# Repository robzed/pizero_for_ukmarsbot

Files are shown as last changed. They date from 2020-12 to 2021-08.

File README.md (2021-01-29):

# Pizero for ukmarsbot
Adding a Rapberry Pi Zero onto the UK Mars Bot

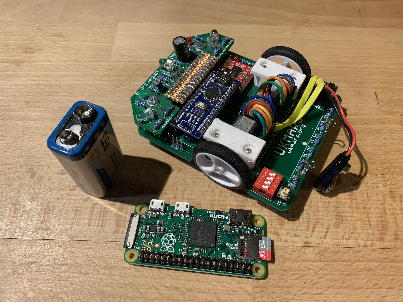
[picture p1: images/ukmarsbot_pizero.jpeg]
UKMarsBot and Pi Zero

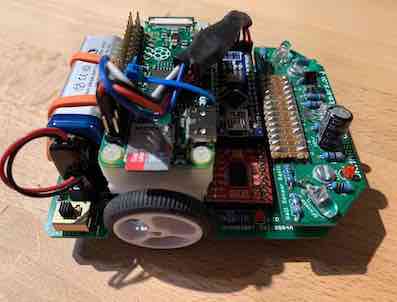
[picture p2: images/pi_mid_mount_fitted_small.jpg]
UKMarsBot_and_Pi
]

NOTE: 

# Background
The UKMarsBot is a maze solver and line follower, designed by the UK Mars and Robotics Society (UKMars). It has a Arduino Nano attached as the standard microcontroller. 

 - GitHub Project page: https://github.com/ukmars/ukmarsbot
 - UKMars Project page: https://ukmars.org/projects/ukmarsbot/
 - Building instructions for the UKMarsBot https://github.com/ukmars/ukmarsbot/wiki

This project aims to add a Raspberry Pi Zero to that basic design.

There is a provisional scope document here UKMARSPIBOT_enhancement_scope.pdf

There is a related seperate GitHub project for the Arduino Nano I/O coprocessor software: https://github.com/robzed/ukmarsey 

# Methods

There are two potential methods of connecting a Raspberry Pi Zero to the UKMARSbot:

1. Produce an adapter board that converts the Pi Zero header to the Arduino Nano footprint, completely replacing the Ardunio Nano. 
2. Connect the Raspberry Pi to the Arduino over a serial interface to the existing Arduino Nano and use the Nano as an I/O processor.

This article will examine the **second** option since this is the simpler option to construct, without a custom PCB. (There are, however, some notes on method 1 provided in '[Replacing the Arduino Nano Entirely](Documentation/Nano_Replacement.md)'.)

# Parts required 
  - UKMarsBot - tested working with Arduino Nano
  - Arduino Nano v3 (or equivalent third-party Nano)
  - Pi Zero v1.3

We will be using a Pi Zero (not a Pi Zero W which uses more power).

# Table of Contents
 - [Powering the Pi Zero … 5v Power … consideration on power](Documentation/Power_Requirements_Detail.md)
 - [What are the options for communicating between Pi Zero and Arduino Nano?](Documentation/Connections_Options.md)
 - [Summary of Electrical Connections between Pi Zero and Arduino Nano](Documentation/Connections_UART_Detail.md)
 - [Installing the Pi Zero Operating System](Documentation/Install_PiZero_OS.md)
 - [Logging into the PI](Documentation/Logging_into_Pi.md)
 - [Disable Linux Console on UART](Documentation/Disable_Linux_Console_on_UART.md)
 - [Scripting language for the I/O processor](Documentation/Pi_and_Nano_Software.md)
 - [Mechanical Mounting - Mounting the Pi Zero onto UKMarsBot](Documentation/Mechanical.md)
 - [Software for the Pi Zero](Documentation/Pi_Zero_Software.md)
 - [Shutdown down the Pi Zero](Documentation/Shutdown_Pi_Automatically.md)
 - [Upgrading the Pi Zero Operating System](Documentation/Upgrading_the_operating_system.md)

# Advanced Topics (Not finished)
 - [Using a Pi Zero W instead of a Pi Zero](Documentation/Pi_Zero_W.md)
 - [Programming the Nano from the Pi Zero](Documentation/Programming_the_Nano.md)
 - [Speed up the Raspberry Pi Boot](Documentation/Speed_up_Pi_Boot.md)
 - [Real time processing on the Raspberry Pi](Documentation/Pi_Real-Time.md)
 - [Reducing Pi Zero Power consumption](Documentation/Reducing_Power_Consumption.md)
 - [Replacing the Arduino Nano Entirely](Documentation/Nano_Replacement.md)
 - [Crazy and Wierd ideas](Documentation/Other_Crazy_Ideas.md)
 - [Remote Debugging Python on a Robot](Documentation/RemoteDebuggingPython.md)

# Other Topcs
 - [Sharing the Internet via OTG](Documentation/Sharing_your_internet_OTG.md)

# Future
 - Increasing the 5v power available to the Pi
 - Fitting a camera

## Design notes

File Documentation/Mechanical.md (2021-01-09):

# Mechanical Mounting - Mounting the Raspberry Pi Zero onto UKMarsBot

To mount the Raspberry Pi securely requires some 3d Printing work.

The design here uses two parts - new motor mounts and the Pi Zero holder which is attached to the motor mounts. These are generated by OpenSCAD using the file ***'rpi_ukmarsbot_mount.scad'***

There are two options provided here (see photos below):
 - A front mount - over the Arduino. This keeps the motors clear, but increases the weight at the front of the Robot - which often is heavy already with sensors. The mini USB connector of the Arduino is still accessible, but the Arduino reset is covered.
 - A mid mount - over the Motors. This means that the weight is more equally distributed over the wheels and this doesn't increase the front weight as much. Any access to the motors or encoders involves removing the Pi Zero.

It might be possible to do a rear mounted, over the battery - but that isn't provided here. 

If you are re-generating the STL files from the OpenSCAD file (say after making a change), the control is generated by the following three settings towards the bottom of the file:
```
SELECT_PI_PLATE_FRONT = false;
MOTOR_MOUNTS = false;
SELECT_PI_PLATE_MID = true;
```
You can also see the whole assembly by selecting the motor mount and one of the two plates.

These are pre-generated STL files:
 * pi_plate.stl (front mount)
 * motor_mounts_only.stl (motor mounts with extra height and holes to fix plates)
 * pi_plate_mid_placement.stl (mid mount)

For fixings, I used M2.5 nylon screws to fix the Pi Zero to 'Pi Plate', and M2 9mm metal screws to fix the Pi plate to the motor mounts. These were fitted screwing into the 3D printed PLA - basically holding by friction fit - it might require some tuning for your specific application. For instance you might need to reduce the holes slightly, or use self-tapping screws.

# Pictures for the Mid Raspberry Pi Mount

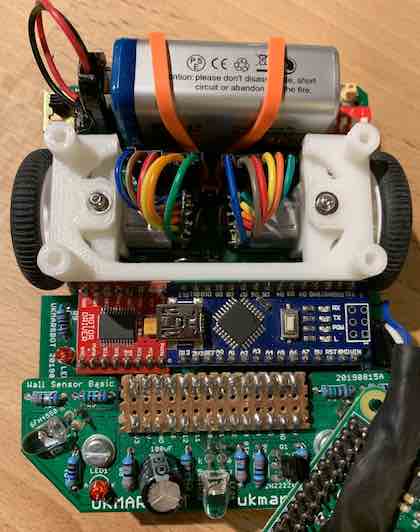
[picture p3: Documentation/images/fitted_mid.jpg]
Fitted Mid

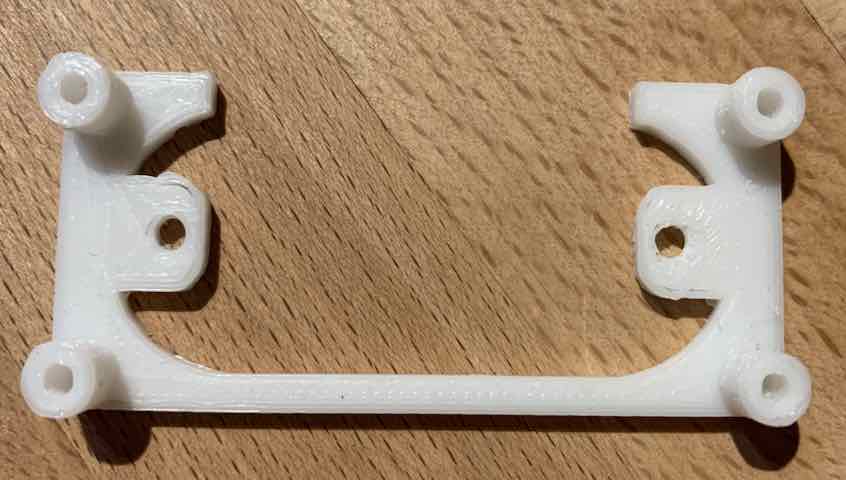
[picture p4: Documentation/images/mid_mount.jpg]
Mid Mount

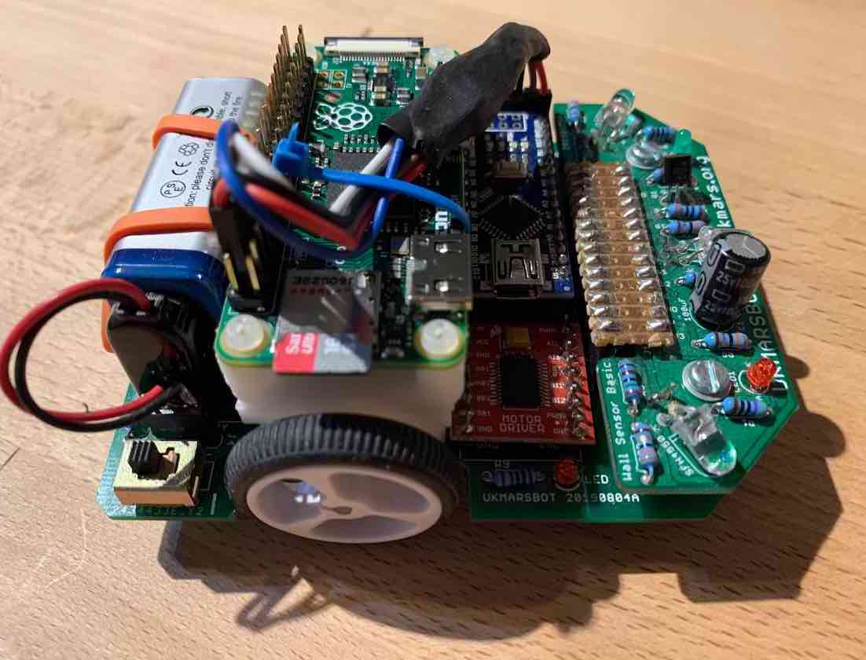
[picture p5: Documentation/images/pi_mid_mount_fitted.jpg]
Mid Fitted 1

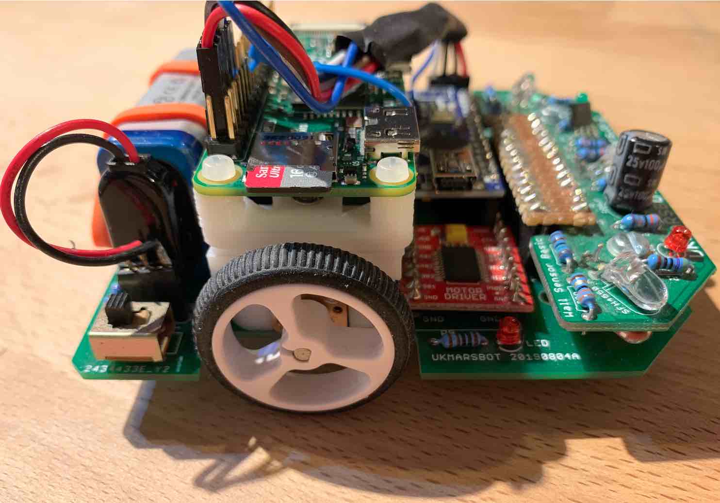
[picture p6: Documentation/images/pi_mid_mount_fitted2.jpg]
Mid Fitted 2

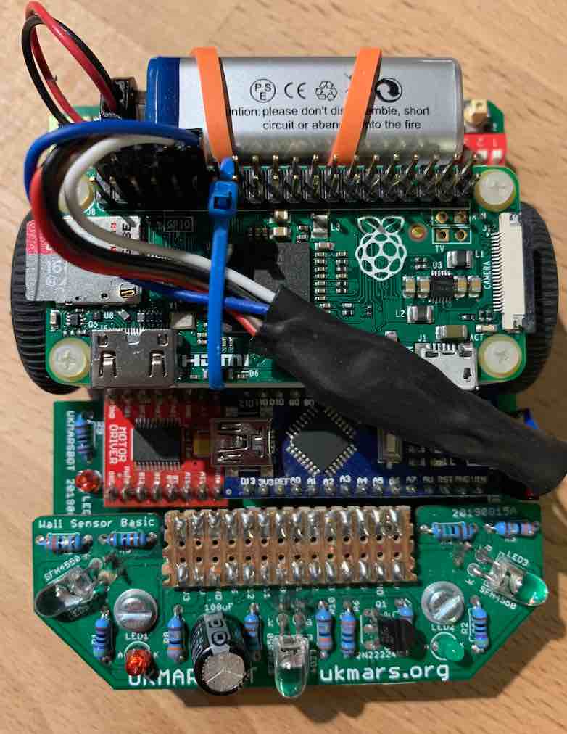
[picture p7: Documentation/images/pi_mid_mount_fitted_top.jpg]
Mid Fitted Top

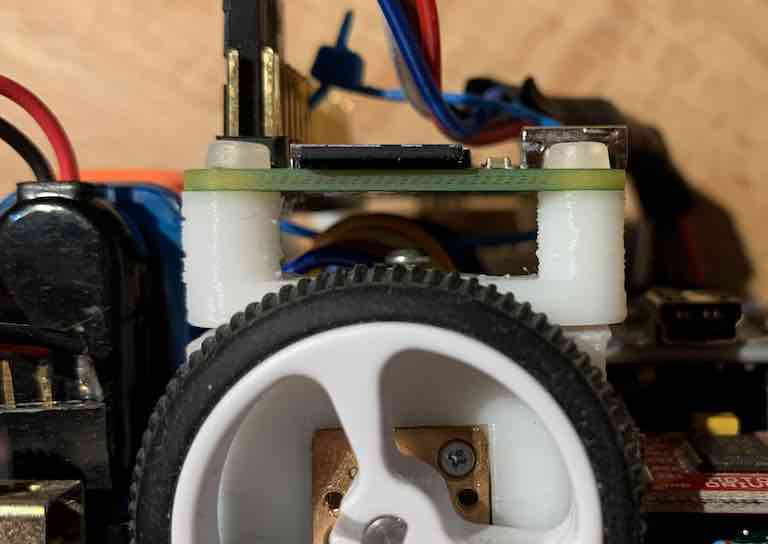
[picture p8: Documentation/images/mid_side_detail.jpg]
Mid Side Detail

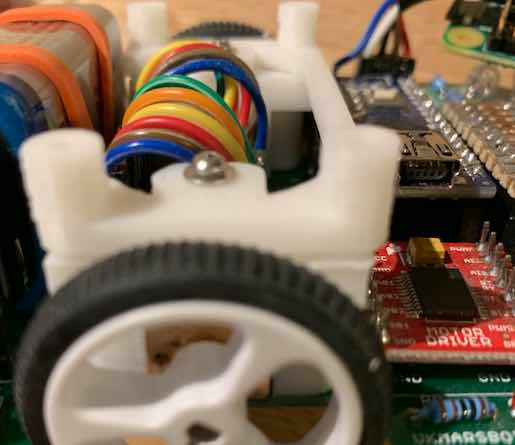
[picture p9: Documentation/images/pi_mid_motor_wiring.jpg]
Motor Wiring


# Pictures for the Front Raspberry Pi Mount

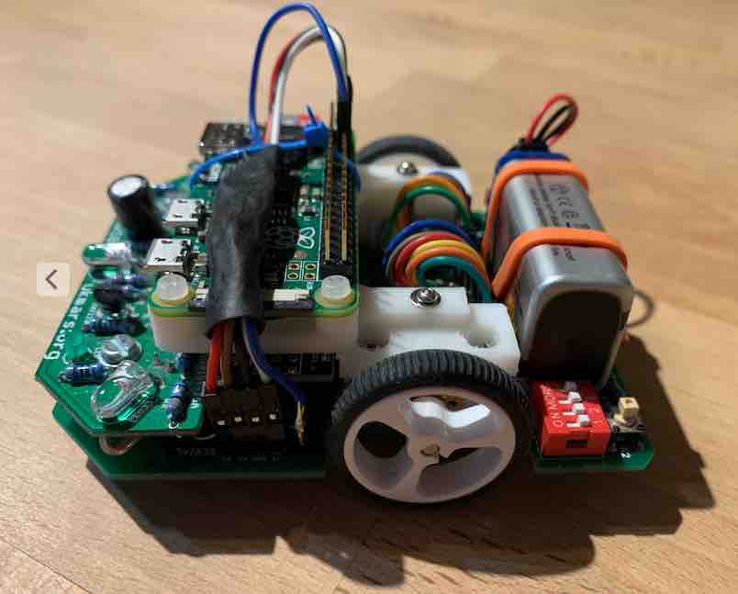
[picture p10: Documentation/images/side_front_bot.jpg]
Side Front Robot

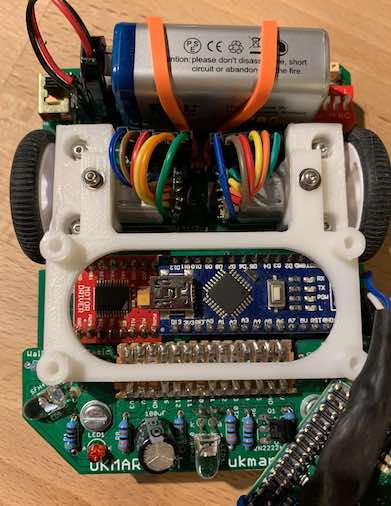
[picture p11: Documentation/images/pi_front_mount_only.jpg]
Front Mount Only

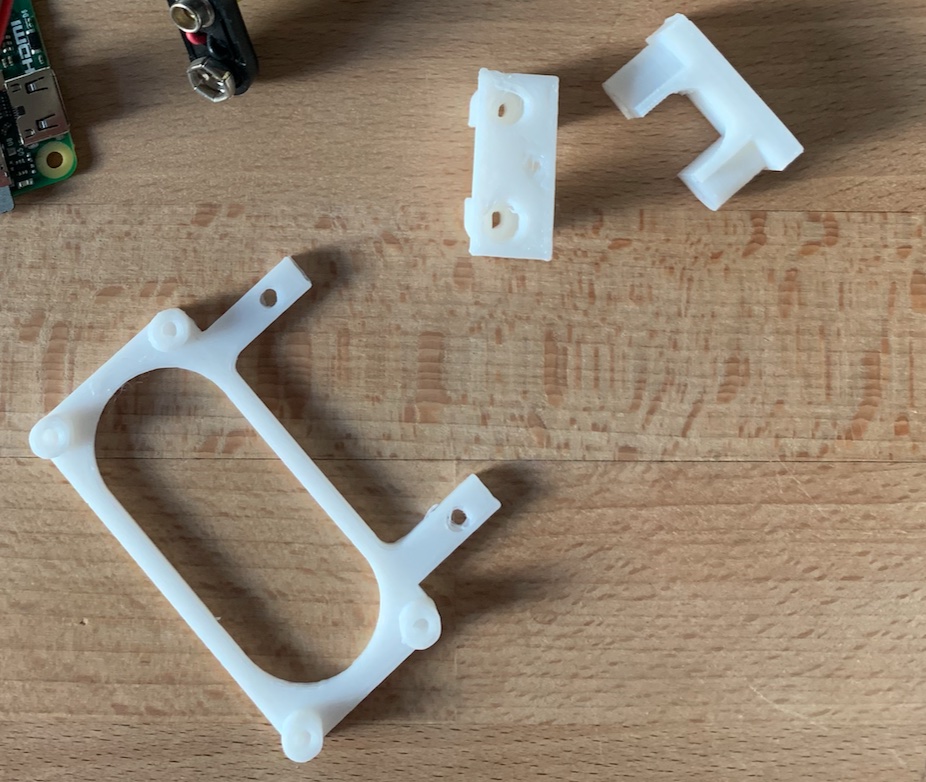
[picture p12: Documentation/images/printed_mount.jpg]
Printed Mount

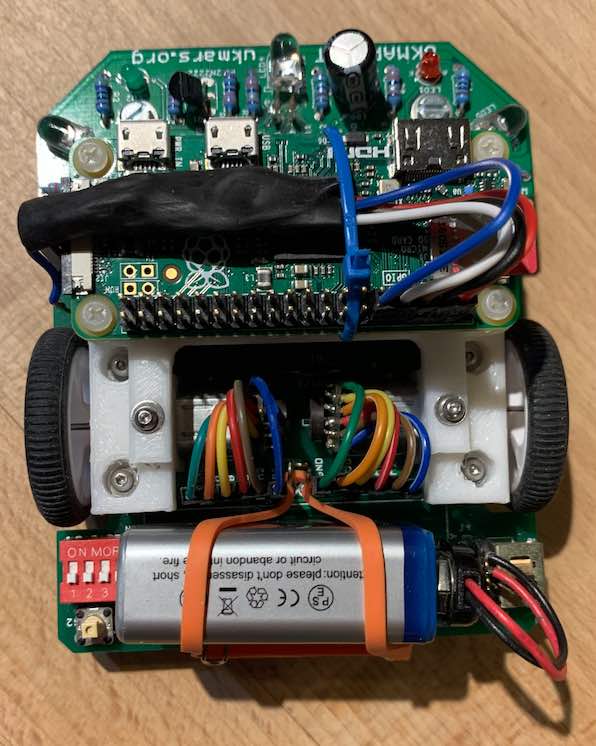
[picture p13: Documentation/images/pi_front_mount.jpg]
Front Mount

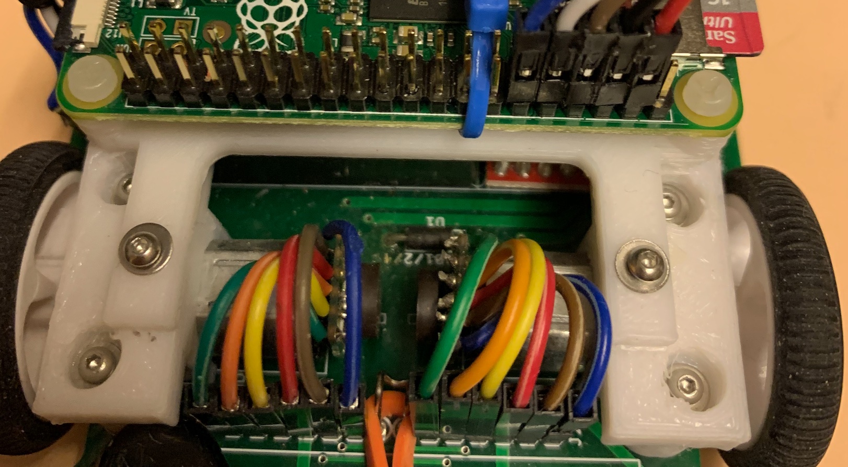
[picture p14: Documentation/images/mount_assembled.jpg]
Mount Assembled

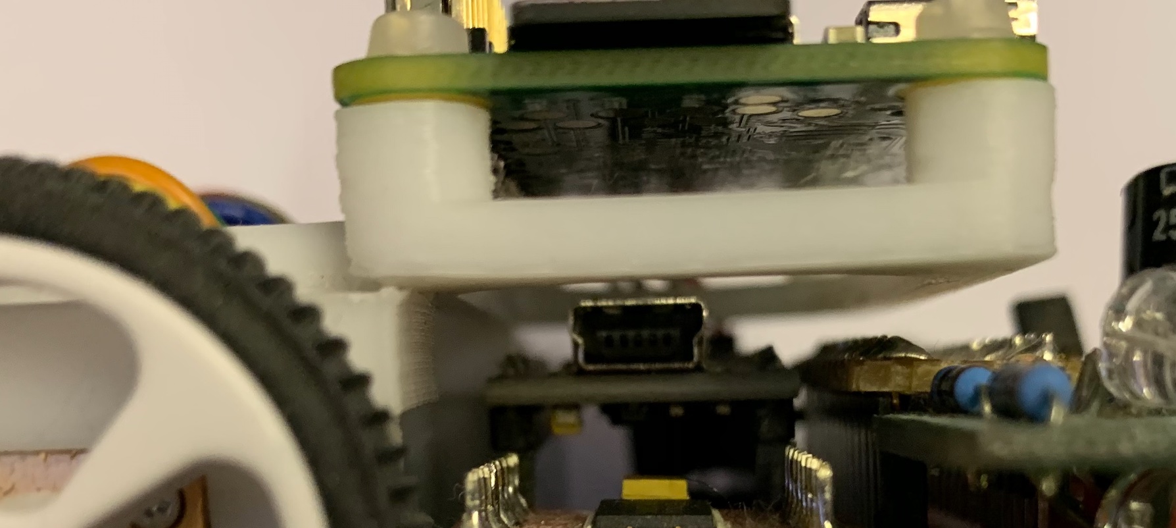
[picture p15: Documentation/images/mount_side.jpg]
Mount Side


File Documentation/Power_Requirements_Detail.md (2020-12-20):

# Powering the Pi Zero

We will power the Pi Zero with 5 volts. The Arduino Nano itself has 5v regulator part number LM1117IMPX-5.0 for the new ones (v3), **Does this have enough additional current to power the Pi?**  Notice some third-party Nano’s use the AM1117-5.0, so we will consider that as well (this is a similar part). 

This is a _linear_ regulator - so the power dissipation is higher when the input voltage is bigger, and it needs to be at least 6.3v for higher currents, otherwise the regulator will start dropping out.

Older Arduino Nano’s used a different regulator - part number UA78M05 - this required 7v input minimum before it stopped regulating properly, and additionally might have different power dissipation. No calculation has been done here.

## Current into the Pi Zero at 5v

The average current of the Pi Zero v1.3 running command line with no GUI, with nothing connected and the HDMI disabled is about 100mA @ 5v, although it might higher on boot - we should assume at least twice that to be safe. It’s possible to reduce that to 80mA by for instance, disabling HDMI.

Please see '[Reducing Power Consumption](Reducing_Power_Consumption.md)' for other details.

Powering the Raspberry Pi Zero doesn’t need to be via the PWR IN Micro-USB power-  we can do this via the 40 way header - pins 2 and 4 are connected to the 5v rail. (Obviously we need to connect the ground / 0v pins as well).

## Calculating the power available for the Raspberry Pi from the Ardunio regulator:

Total current **theoretically** available using LM1117IMPX-5.0 = 800mA

Total power **theoretically** available using AM1117-5.0 = 1A

However, the limiting factor is the power dissipation of the package. Since they are linear regulators they get rid of the ‘extra voltage’ (actually extra power) by dissipating it as heat. If you run your UKMARSbot with a Nickel Metal Hydride 9v battery, then it might (when fully charged) sit at 9v (on load, offload it can be higher) - although normally it's about 8.5v. To get down to 5v involves getting rid of all 4v times the current in heat. This is because P = IV (Power equals current times voltage).

The current of the Arduino is probably something like 33mA@5v (or 167mW), but we also need to take account of all 5v and 3v3 usage of the UKMARSBot. This adds up to about 49 mA to 66mA depending upon LEDs @ 5v. (The Arduino can theoretically use I/O to up 233.4mA as well, and we have to assume you don’t leave the IR LEDs on all the time…)

https://arduino.stackexchange.com/questions/926/what-is-the-maximum-power-consumption-of-the-arduino-nano-3-0

The currents looks well within the limits of the 5v regulator - even during boot up, but we also need to consider power dissipation. 

The LM1117 data sheet has a graph  “Figure26. Maximum Allowable Power Dissipation vs Ambient Temperature for SOT-223”. If the ambient temperature is 25 degrees C, then we can get between 800mW and 1.4W depending upon how good the heat sink created by ground plane  - and usually it’s not as good!

At 800mW, dissipating 4v (worst case) at 100mA for the  Pi Zero (Let’s ignore the initial boot up current - and assume the regulator will take a while to get up to 125 degrees C), and then 66mA for the Ardunio and I/O, sensors, etc. 

So 166mA * 4v = 664mW. This gives us some margin (20%) assuming that the power dissipation of the package on this PCB is 800mW. 

NOTICE: The regulator part (which is located on the underside of the Arduino Nano) might get hot at this current - and care should be taken to avoid getting burnt - but usually it’s out of reach when plugged into the UKMarsBOT.

## Other Power notes

The Pi Zero v1.3 has a PAM2306AYPKE, which is a buck regulator for 1.8V/3.3V. Buck regulators are quite efficient (to up 96%) and this means lower currents. NOTE: Earlier Raspberry Pi’s had linear regulators - and these will lead to higher currents. 

Other peripherals (cameras, keyboards, mice, etc.) will greatly increase power usage and current drawn. Do not connect cameras and record video! https://raspi.tv/2017/how-much-power-does-pi-zero-w-use

## IMPORTANT NOTE

If you want to use more features on the Pi Zero, or a Pi Zero W (and Bluetooth from computer and mobile phone is cool, as is a network) - then you will need to calculate whether there is enough current avaialble at 5v, or add a second regulator.

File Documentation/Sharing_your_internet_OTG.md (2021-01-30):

# Sharing your Internet with the Pi Zero via OTG

## Mac

System Preferences > Internet Sharing

First you have to select RNDIS/Ethernet Gadget then Internet Sharing

Make sure you have selected where you have sleected where to share your internet connection from!

https://raspberrypi.stackexchange.com/questions/47678/rndis-ethernet-gadget-share-internet

NOTE: Internet sharing can stop sleep while enabled, especially if connected to AC Power.

## Windows

**todo**

## Linux Dekstop

**todo**

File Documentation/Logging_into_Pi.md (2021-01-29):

# Logging into the PI

Obviously you could connect to the Raspberry Pi with a monitor, keyboard and mouse - but this is a bit pain.

Since we’ve used the UART for communication to the Ardunio Nano, we can’t log in via serial either.

However, the Pi Zero (only) supports OTG mode, where you can connect it directly to the USB of your computer and access via SSH or VNC. To do this you need to prepare the SD card before you boot it:

For this method, alongside your Pi Zero you will require:
 - MicroUSB cable (USB-A one end to insert into your computer, micro-USB another - to insert into the Pi Zero),
 - MicroSD card (that you programmed with Raspberry Pi OS),
 - a computer which can be running Windows (with Bonjour, iTunes or Quicktime installed), Mac OS or Linux (with Avahi Daemon installed, for example Ubuntu has it built in).

Then do the following:

1. Once Raspbian is flashed, open up the boot partition (in Windows Explorer, Finder etc) and add to the bottom of the 'config.txt' file dtoverlay=dwc2 on a new line, then save the file.
2. If using a recent release of Jessie (Dec 2016 onwards), then create a new file simply called ssh in the SD card as well. By default SSH is now disabled so this is required to enable it. Remember - Make sure your file doesn't have an extension (like .txt etc)!
3. Finally, open up the cmdline.txt. Be careful with this file, it is very picky with its formatting! Each parameter is seperated by a single space (it does not use newlines). Insert modules-load=dwc2,g_ether after rootwait. To compare, an edited version of the cmdline.txt file at the time of writing, can be found in the references below.
4. That's it, eject the SD card from your computer, put it in your Raspberry Pi Zero and connect it via USB to your computer. It will take up to 90s to boot up (shorter on subsequent boots). It should then appear as a USB Ethernet device. You can SSH into it using raspberrypi.local as the address.

## Some references:
- https://gist.github.com/gbaman/975e2db164b3ca2b51ae11e45e8fd40a
- https://blog.gbaman.info/?p=791
- https://raspberrypi.stackexchange.com/questions/38827/how-to-connect-raspberry-pi-zero-to-pc#38828
- https://www.novaspirit.com/2016/10/18/raspberry-pi-zero-usb-dongle/

If you are using *Windows*, you’ll need to install Bonjour.

You can connect to the Rasberrry with a USB cable with a microUSB end plugged into the USB Pi Zero connection (NOT PWR IN). NOTE: Make sure it’s a data cable, not just a charge cable. (One way to test this is to use a Android phone with the cable …)

Because of Bonjour, you can probably directly SSH into the Pi Zero.

More information here especially about Windows: https://learn.adafruit.com/turning-your-raspberry-pi-zero-into-a-usb-gadget/ethernet-gadget

To SSH into your Raspberry Pi you can do this on Linux and Mac

    ssh pi@raspberrypi.local

On Windows, you can use any program that supports SSH, for example Putty, WinSCP, or Teraterm. The address should be raspberrypi.local and the user is 'pi'. 

Password will be default **raspberry**

NOTE: It will give you a warning, since we are using the default password.

The time and date will not be set. If this bugs you, type:

    sudo date -s "6 Dec 2020 22:36"

If the board gets network access, then NTP will synchronise the time.

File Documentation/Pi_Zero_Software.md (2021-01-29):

# Pi Zero Software

# Summary

Jobs need to be split between the Arduino Nano and the Raspberry Pi Zero.

We want to use the Raspberry Pi processing power and large RAM to do as much as possible, but there are some constraints we need to be aware of as we design the software:
 - We don't have instance access to the sensors and motors from the Pi Zero, and this means we need to do fast operations with low latency on the Arduino Nano.
 - We need to make sure that the Raspberry Pi isn't busy which holds up commands to the Arduino Nano.
        - The SD Card especially is slow to read and write and can delay the program.
 - The serial link between the Pi Zero and Nano is slow - and therefore:
    - Introduces latency between sensor data and actions
    - We need to make sure sensor data and commands are as small as possible. (It will be nice to make them human readible, however, for ease of debugging).
 - The basic Nano only has 2 KByte of RAM and 32 KByte of Flash. 
   - (Although the Arduino Nano has 1KByte of EEPROM, it seems useless when we have an SD Card on the Raspberry Pi - as long as we defer writes till after runs.?)
 - The Pi Zero only has a single processor.
 - The UART is full-duplex (can send and receive simulataneously) - and we should leverage this to minimise latency.

# Overview
The Pi Zero needs software to:

 * Talk to the Ardunino and tell it what to do
 * Process information from the Arduino (e.g. batteries, sensors, switches, etc.)
 * Decide when to stop (e.g. when batteries are too low, or we have complete the mission).
 * Decide when to shutdown the Pi Zero.

# Setup Python serial library

We will use Python 3 here. If you try to import serial you will probably get an error:

    python3
    pi@raspberrypi:~ $ python3
    Python 3.7.3 (default, Jul 25 2020, 13:03:44) 
    [GCC 8.3.0] on linux
    Type "help", "copyright", "credits" or "license" for more information.
    >>> import serial
    Traceback (most recent call last):
      File "<stdin>", line 1, in <module>
    ModuleNotFoundError: No module named 'serial'
    >>> quit()

So you'll need to install it for Python 3. Let's do it via pip3. You need network access - so if you are just using on the OTG you need to make sure you have network access. There is information here [Sharing the Internet via OTG](Documentation/Sharing_your_internet_OTG.md)

    sudo apt-get install python3-pip

Then install pyserial

    sudo pip3 install pyserial

Then:

    pi@raspberrypi:~ $ python3
    Python 3.7.3 (default, Jul 25 2020, 13:03:44) 
    [GCC 8.3.0] on linux
    Type "help", "copyright", "credits" or "license" for more information.
    >>> import serial
    >>> port = serial.Serial("/dev/serial0", baudrate = 115200, timeout = 0.1)
    >>> print(port)
    Serial<id=0xb6687d10, open=True>(port='/dev/serial0', baudrate=115200, bytesize=8, parity='N', stopbits=1, timeout=0.1, xonxoff=False, rtscts=False, dsrdtr=False)
    >>> port.inWaiting()
    0

If you have a problem accessing the serial, you might need to give the 'pi' user access - the group is 'dialout'. You can check with the groups command. 

    pi@raspberrypi:~ $ groups
    pi adm dialout cdrom sudo audio video plugdev games users input netdev gpio i2c spi

You can add the 'pi' to the group with:

    sudo adduser pi dialout

For other users replace pi with the user name. 

**(This is not finished yet)**

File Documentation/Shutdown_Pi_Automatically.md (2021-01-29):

# Shutting Down the Raspberry Pi Automatically

If you just turn the switch off the UK Mars Bot, then there is some chance - if it’s written to the SD card (always possible) that you will corrupt the SD card and will need to refresh it. 

Obviously you could plug in a USB cable and issue “sudo shutdown -h now” or “sudo poweroff”, but it’s not very convenient. (Wait for the LED to stop flashing and go out).

It’s much better to read the switches on the UKMARSBot and shutdown the Pi Zero that way - based on the program in the Raspberry Pi. This can either be by the press-button or switches, but also probably needs to be when the battery is low.

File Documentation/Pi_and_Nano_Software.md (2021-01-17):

# Getting the New Nano+Pi Zero to do some stuff

We will use a low overhead serial protocol based on the command line here https://github.com/robzed/ukmarsey

Please visit that project for details - this what needs to be programmed into the Arduino Nano for the robot to function.

The Python program in this project will talk to that software.

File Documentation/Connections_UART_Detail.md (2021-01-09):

# Summary of Electrical Connections between Pi Zero and Arduino Nano

The basic connections are: 

 1. Ground - ideally several ground points will prevent problems with power and data
 2. 5v
 3. TX - data transmit
 4. RX - data receive

NOTE: This leaves many pins free for other uses on the Raspberry Pi Zero!

Connection header - The UK MARS Bot provides a 4 pin header with the above connections. Although it only contains a single ground, it’s probably good enough to experiment with as long as the header is tight.

Nano TX / Pi Zero - voltage conversion to protect the Pi Zero receive - two resistors will change the voltage level from 5v on the Nano to 3v on the Raspberry Pi. 3k3 ohm connected to ground, 2k2 connected to Nano TX. 

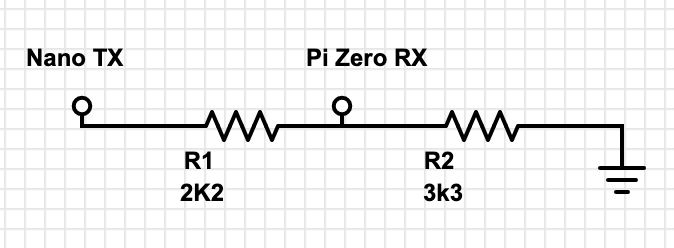
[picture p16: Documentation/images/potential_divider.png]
Converting 5v TX to 3v3 RX


The TX from the Pi Zero will be ok to be wired into the Nano RX pin - the voltage levels are safe, and the voltage level should be high enough to trigger the input.

## Nano RX override

Obviously if we are using the UART to communicate to the Nano, when reprogramming the Nano, we need to disable the transmit pull up from the Pi Zero so that the USB chip can pull down the RX line on the Nano (through the 1K resistor).

There are three options:

1. Overriding the USB converter, but allowing it to program the Arduino Nano. This will require a Schottky diode - say 1N5817 - to make the raspberry Pi TX only pull down the input. As long as both the programmer and the Raspberry Pi are not communicating at the same time, this approach will work.

2. Remove the Raspberry Pi serial connections before programming the Arduino Nano.

3. Get the Raspberry Pi to program the Arduino Nano.

The second option 2 what I will use, but the diagram below shows the optional diode required from option 1.

## Raspberry Pi GPIO Header - UART and Power

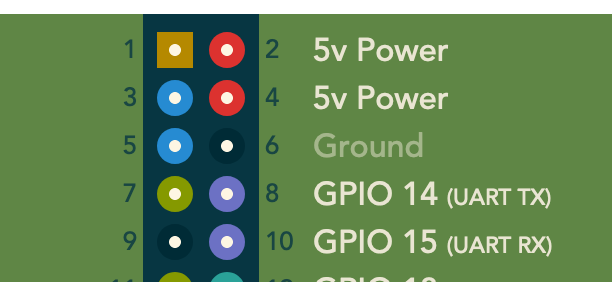
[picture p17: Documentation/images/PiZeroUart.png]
Pi Zero Header UART detail


(from https://pinout.xyz/pinout/io_pi_zero)

## UKMarsBot Serial Header

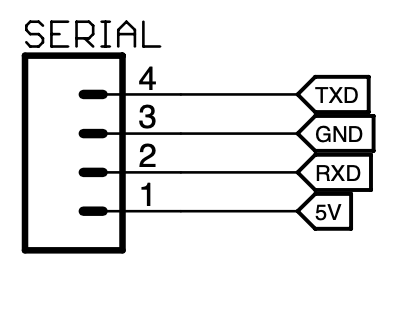
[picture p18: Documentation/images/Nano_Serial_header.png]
Nano Serial Header


## Wiring up the two units

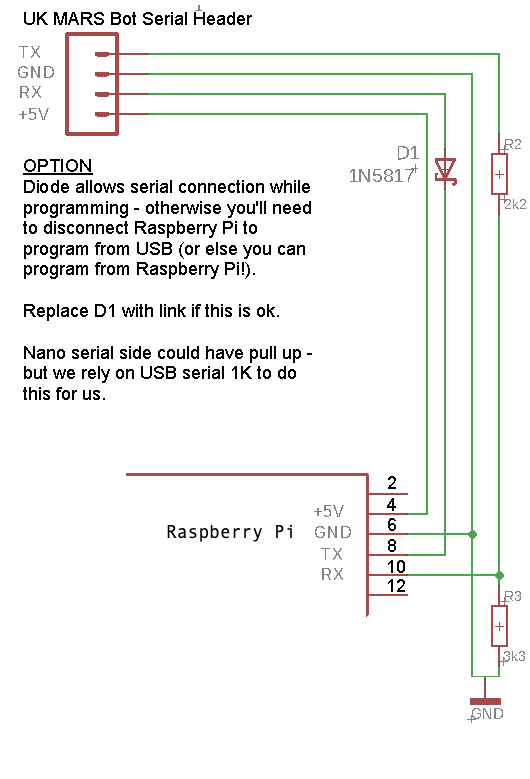
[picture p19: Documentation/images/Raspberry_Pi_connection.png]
UK Mars Bot Serial to Pi Zero schematic wiring diagram


## Images 

The images show: Red (+5V), Brown (Rx - Receive to Arduino), Black (0v/Ground), White (Tx - Transmit from Arduino).

Notice some of these images show an addition blue wire. This is connected (via a schottky diode) to the reset pin - thoeretically so a GPIO on the Pi Zero can pull down and reset the Arduino for programming. The diode avoids the GPIO on the Pi Zero pulling up or fighting the other part of the circuit. This method of resetting has not been tested.

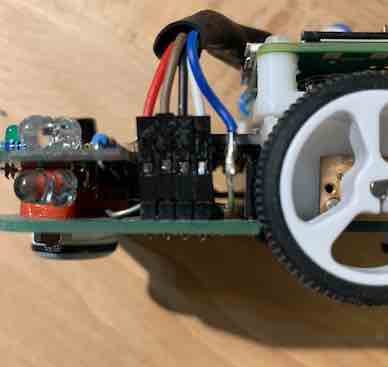
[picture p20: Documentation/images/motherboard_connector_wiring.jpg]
Motherboard View of Connections

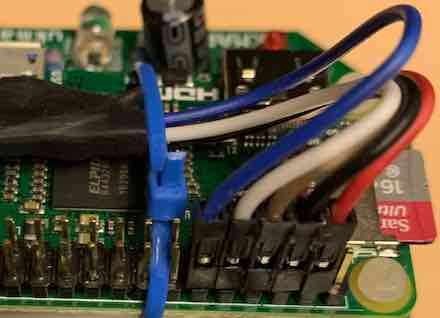
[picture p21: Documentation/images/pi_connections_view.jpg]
Pi Connections View


This shows the two resistors, basic soldering for the inline lead. The yellow, green and blue sleeving is heat shrink tubing and it will be moved over the solder joins and protect the wires from shorting. The final assembly had larger black heat shrink tubing over all the wires - you can see this on the other images (e.g. on the mechanical pages).
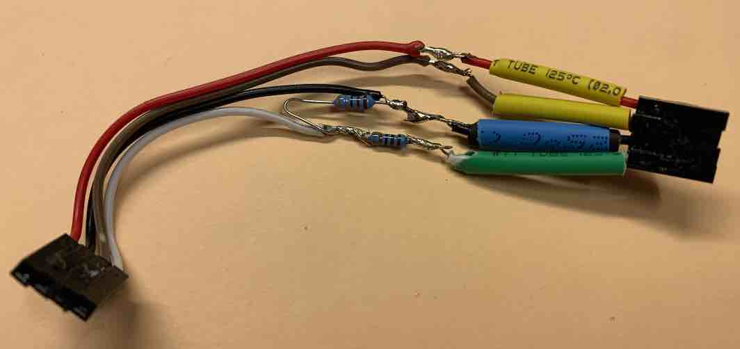
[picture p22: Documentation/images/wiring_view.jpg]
Wiring Loom


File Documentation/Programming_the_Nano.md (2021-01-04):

# Programming the Arduino Nano from the Raspberry Pi Zero

** This is work in progress and has not been tested yet **

You will need an extra GPIO line on the Raspberry Pi, and a schottky diode connected between that GPIO and Pin 3 on the Ardunio Nano. (The alternative is a logic shift gate or a transistor).

We will use Pin 12 which is GPIO 18. This is right next to the serial connections - so we can use one 5 pin header. In fact, in an ideal situation we could use a 7 pin header so that we have two Ground connections and two 5v connections (Pins 2, 4, 6, 8, 10, 12, 14). That will ensure good grounding and power at the raspberry pi end.

(The alternative is another like that can be used as a DTR pin.)

At the UKMARSbot there is no reset at a header - so we will need to solder a wire onto pin 3 of the Arduino Nano and provide our own connection method.

## Theory of operation

When the Raspberry Pi outputs a logic zero, the drop is low enoguh across the schottky diode to pull down the reset and ensure the Arduino resets. That way the Raspberry Pi  can start

*(Add schematic diagram - todo !)*

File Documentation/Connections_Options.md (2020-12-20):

# Communication between the micros

**IMPORTANT NOTE:** The Arduino Nano is 5v I/O and the Raspberry Pi is 3v I/O. Care needs to be taken when connecting one to another.

## Option 1 - UART serial lines

Serial: 0 (RX) and 1 (TX). Used to receive (RX) and transmit (TX) TTL serial data. These pins are connected to the corresponding pins of the FTDI USB-to-TTL Serial chip. However, there is a 1 Kohm connection, and so these signals can be overridden by other uses.

Some UKMARS users have this also used for debugging in real-time via a Bluetooth module. This will not be possible if we use these serial lines to talk to the Pi Zero.

## Option 2 - I2C Interface

This is a two wire protocol, which is tracked to A4/A5 and then to  sensor boards, but unused on the current v1 sensor boards. 

However using this interface would step the ability to connect advanced sensor boards using I2C or other analogue inputs.

## Option 3 - SPI Interface

This is tracked to D10, D11, D12, D13. These are mostly used for other functions on the UKMARSBot which don’t make them ideal. A considerable amount of changes would be required - therefore this is discounted from this guide. Adventurous experimenters might consider this interface, however.

## Option 4 - USB interface

This uses the Raspberry Pi as the host interface, and the Arduino nano as the device / peripheral.

This is a reasonable approach - but I have questions about power (the Arduino has power, the Raspberry Pi doesn’t - so maybe a separate power connection needs to be made. Additionally reprogramming the Arduino either need to be done via the Raspberry Pi, or the connection must be disconnected.

A third issue is that connecting to the Raspberry Pi would also use this port in OTG mode.

## Conclusion

Because the Raspberry Pi and Arduino Nano UART serial port is free, except for programming, and both ends are easy to debug on a PC without extra tools, this is the approach we will take.

NOTE: Without somehting like Bluetooth from the Arduino Nano, any debug data will need to be transmitted to the Raspberry Pi - however, since it has quite a lot of memory, we can store it in the Raspberry Pi RAM (then write to SD card after the robot has completed it's real-time movements).

## Things we need to take care of:

1. Ensure that we can still program the Arduino when required via the USB interface (that still uses this UART serial inter
2. We need to be careful how we power off the mouse, or we will need to write-protect the SD card after initial boot (can be done from software) - otherwise the SD card will become corrupt.
3. Ensure that the 5v transmit line of the Arduino doesn’t damage the Raspberry Pi. 
4. Disable the Raspberry Linux Pi console UART so that doesn't interfer with our communication.
5. Provide a communication protocol between the two devices.

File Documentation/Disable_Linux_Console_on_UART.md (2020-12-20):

# Avoiding the Linux Serial Terminal Console

Normally there serial terminal console on pins 8 and 10 can be used to login. This will interfer with the communication to the Nano so must be disabled. 

To disable this the easiest way is to log onto the Raspberry Pi:

Then use raspi-config as follows:
1. Start raspi-config: *sudo raspi-config*.
2. Select option 3 - Interface Options.
3. Select option 6 - Serial Port.
4. At the prompt *'Would you like a login shell to be accessible over serial?'* answer 'No'
5. At the prompt *'Would you like the serial port hardware to be enabled?'* answer 'Yes'
6. Exit raspi-config and reboot the Pi for changes to take effect.

For other methods, see here: https://elinux.org/RPi_Serial_Connection#S.2FW:_Preventing_Linux_from_using_the_serial_port

References
https://www.raspberrypi.org/documentation/configuration/uart.md

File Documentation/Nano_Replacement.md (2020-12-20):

# Replacing the Arduino Nano entirely with a Pi Zero

This information is provided for information only, and shoudl be considered provisional.

**(This is not finished yet)**

## General approach

It's probably worth creating a daughterboard that connects into the Arduino nano footprint and also allows the 40-way Raspberry Pi header connected. 

## Add link to info about 3v3 change (e.g 74HCxx rather than 74LSxx)

This UKMarsBot v1 was designed to use 5v, however, some work has been made on running it on 3v aleady.

## 5v regulator

The Raspberry Pi Zero requires a 5v supply - which can be provided via one micro USB headers or via the 5v pins on the GPIO header.

Possible options are:
 - DC-DC converter - this is probably the best option

## ADC - Analogue to digital converter

## Add link to info about PWM

## Other notes (add in above)
Provide an ADC - potentially with a serial interface like I2C or SPI.
Provide a 5v regulator.
Convert the UKMARS I/O to 3v3. This is not overly problematic- - the http://ukmars.org site details this for other boards (like the Arduino Nano 33 BLE).
Figure out how to route a PWM signal to the motors for speed control.

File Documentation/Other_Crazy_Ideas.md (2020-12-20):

# Other Crazy Ideas

This is a list of ideas that are off-the-wall, for your inspiration.

- With a Pi Zero W and a NanoBLE or Nano33BLE, you could avoid having a communication wire, and instead communicate over BLE. Of course you'd still need a power wire...

**(This is not finished yet)**

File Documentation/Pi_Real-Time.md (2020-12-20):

# Information on Raspberry Pi Programming - with Soft Real-time

Real-time on the Pi Zero is tricky without care. We won't get into high preicision timers (standard) or the RT-PREMPT patch (not standard) here - and that's ok because we have the Ardunino Nano to do very fast real-time actions.

However, it's important to consider what might hold up the Raspberry Pi.

The mouse might crash if it doesn’t perform in the correct operation in time, or at least be non-optimal. It’s still possible, without major changes, to convince the Raspberry Pi’s Linux operating system to perform well enough, without special changes (like preemptive kernel threading) or low level drivers.

## SD Card access

If you write to SD card then the program may pause, and the same is true of reading. Try to use only RAM during running the robot and save or load once it’s stopped.

## Real-time threads

Linux by default supports a thread type called real time threads. These are higher priority than normal threads, and it can help get better performance.

**(This is not finished yet)**

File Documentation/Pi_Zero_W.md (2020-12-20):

# Pi Zero or Pi Zero W

If you want to use a Pi Zero W instead of a Pi Zero there are several differences:
 - It uses more current <add details>
 - The UARTs are swapped around, depending on which device you refer to.

Comparison between Pi Zero and Pi Zero W https://raspi.tv/2017/how-much-power-does-pi-zero-w-use

https://lifehacker.com/how-much-power-the-raspberry-pi-zero-w-uses-compared-to-1792854782

At about 20mA more, you probably can get away with running a Pi Zero W ...

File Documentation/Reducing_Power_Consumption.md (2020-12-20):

# Reducing Power Consumption

## Basic Options

To quote from https://www.jeffgeerling.com/blogs/jeff-geerling/raspberry-pi-zero-conserve-energy

| Technique | Power Saved | Notes |
| -- | -- | -- |
| Disable HDMI | 25mA | If you're running a headless Raspberry Pi, there's no need to power the display circuitry, and you can save a little power by running /usr/bin/tvservice -o (-p to re-enable). Add the line to /etc/rc.local to disable HDMI on boot. |
| Disable LEDs | 5mA per LED | If you don't care to waste 5+ mA for each LED on your Raspberry Pi, you can disable the ACT LED on the Pi Zero.|
| Minimize Accessories | 50+ mA | Every active device you plug into the Raspberry Pi will consume some energy; even a mouse or a simple keyboard will eat up 50-100 mA! If you don't need it, don't plug it in. |
| Be Discerning with Software | 100+ mA |  If you're running five or six daemons on your Raspberry Pi, those daemons can waste energy as they cause the processor (or other subsystems) to wake and use extra power frequently. Unless you absolutely need something running, don't install it. Also consider using more power-efficient applications that don't require a large stack of software (e.g. LAMP/LEMP or LEMR) to run.|

## Detail

Disable HDMI saves 25mA

You can also disable the ACT LED … but this seems to be useful to spot shutdown and other SD card operations - It’s only 5mA. In my opinion it's not worth it.

“sudo raspi-config” option 1: System Options.

**(This is not finished yet)**

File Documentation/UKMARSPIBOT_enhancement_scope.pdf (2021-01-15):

Ian Butterworth | V2 14 January 2021 | Page 1 of 2

## Definition of scope for a UKMARSBOT enhancement

### 1. Concept

Extend the hardware and software of the UKMARSBOT platform to enable builders to control the UKMARSBOT and have programmatic access to the interface connector using a Raspberry Pi processor board.

### 2. Purpose

The preferred computer learning platform for many schools, colleges and hobbyists is the Raspberry Pi. Competitions such as Pi Wars are popular with robot builders.

Extending the capability of the UKMARSBOR platform to include control by a Raspberry Pi will significantly widen the potential audience for UKMARSBOT and provide Pi based builders with a capable platform as a basis for their projects for Raspberry Pi based competitions.

Implementing this enhancement will also allow builders using the Raspberry Pi to build robots capable of completing UKMARS sponsored challenges of Maze Solving, Wall Following, Line Following and Drag Racing.

### 3. Outline of capabilities

The idea is to provide:
- a programmable running chassis with the capability to mount small wheels inboard and large wheels outboard to meet the requirements of many robotics challenges
- programmable access to the sensor board interface on the UKMARSBOT to support the use of existing sensor boards or the control of new boards with different sensor/actuator configurations
- the necessary mounting hardware to fix a Raspberry Pi Zero or ZeroW to the UKMARSBOT
- consider including mounting for a Pi camera
- instructions and guidance on connecting the Pi to the on-board Arduino through a serial connection
- instructions and guidance on supplying power to the Pi
- definition of the protocol and commands that are supported on the serial connection
- software for the on-board Arduino to implement the commands and protocol over the serial connection. This Arduino software to be viewed as firmware with builder software confined to the Pi using the subsystem through the serial interface
- UKMARSBOT is an open source project, advanced builders may, if they wish, modify the Arduino firmware and undertake distributed development, though this should not be necessary to build working robots

### 4. Challenges the platform could support

The platform could provide the basis for multiple challenges so long as builders add specific hardware to perform the bespoke challenges.

All the 2021 Pi Wars contests:
- Feed the fish
- Tidy up the toys
- Up the garden path

Ian Butterworth | V2 14 January 2021 | Page 2 of 2
- DIY obstacle course – may be trickier with just 2 wheels

Pi Wars 2020 challenges:
- Lava Palava
- Eco Disaster
- Escape Route
- Minesweeper

UKMARS contests:
- Line following
- Wall following
- Maze solving
- Drag racing

IET Competitions:
- Line following
- Time trial
- Drag racing

Other contests:
- Sumo (with 2 wheels?)

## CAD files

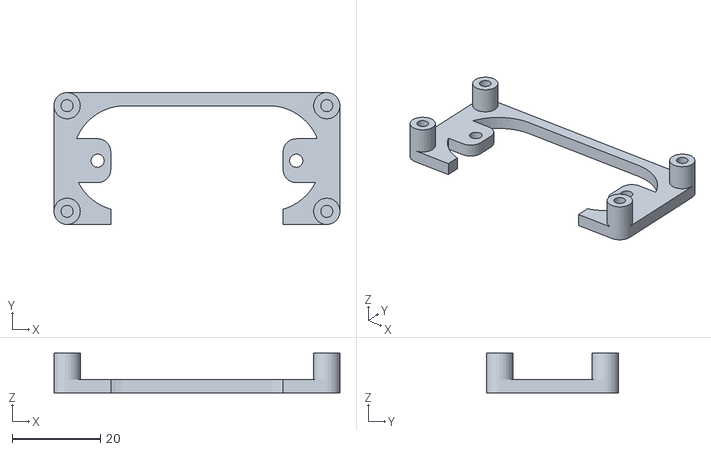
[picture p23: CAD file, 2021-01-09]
mechanical/pi_plate_mid_placement.stl
65.0 x 30.0 x 9.00

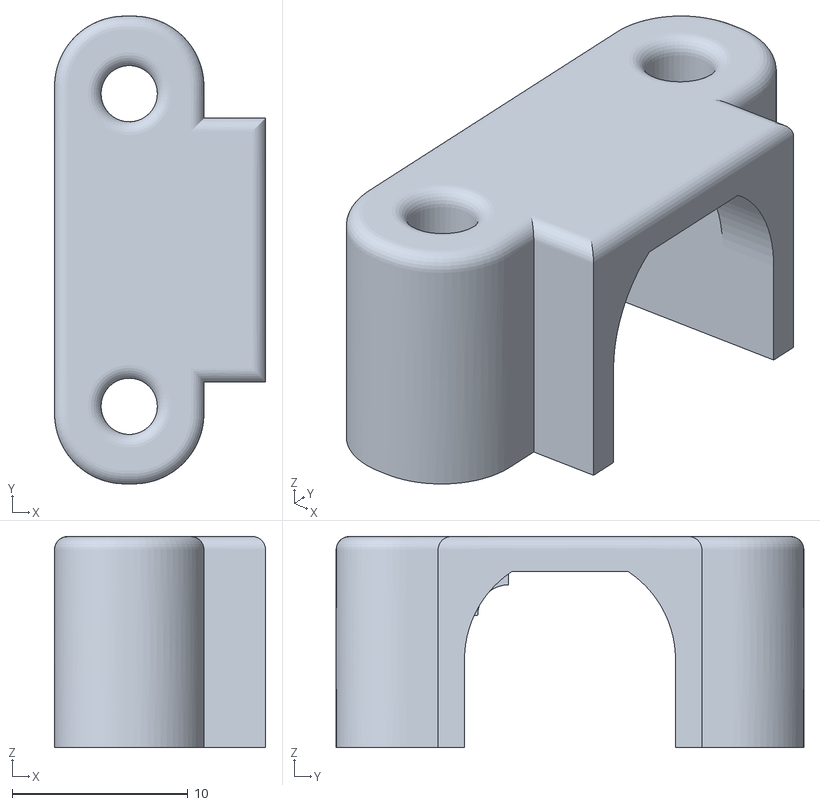
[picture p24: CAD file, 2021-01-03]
mechanical/submodules/pololu-gear-motor-bracket-standard.stl
12.0 x 26.6 x 12.0

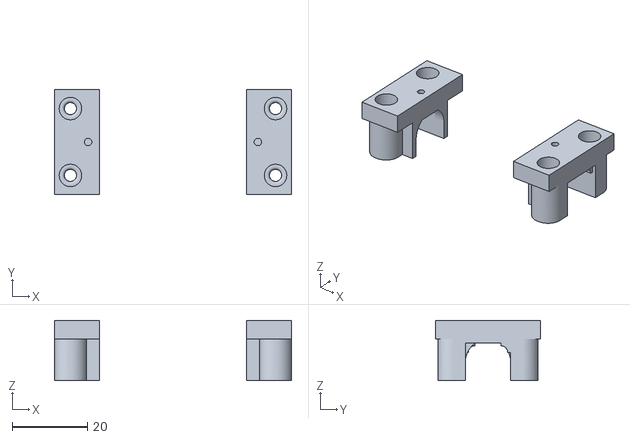
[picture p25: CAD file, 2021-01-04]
mechanical/motor_mounts_only.stl
63.1 x 28.0 x 16.0

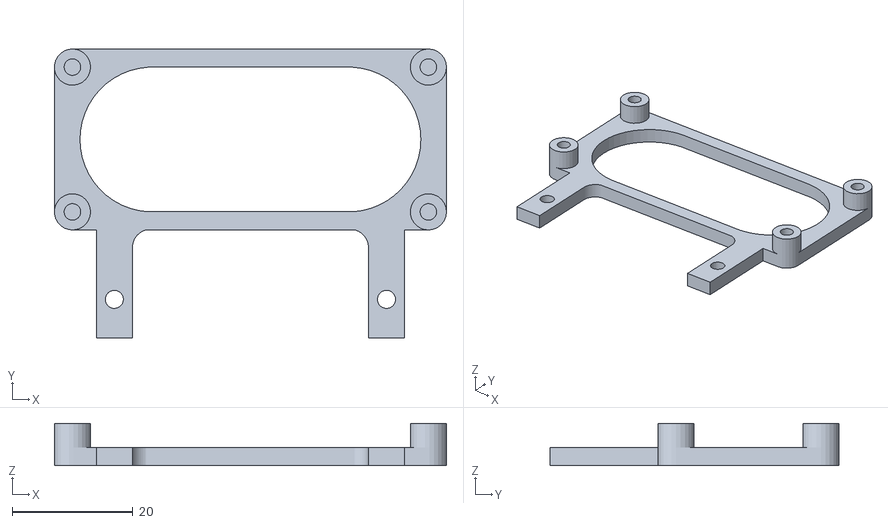
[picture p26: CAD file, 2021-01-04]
mechanical/pi_plate.stl
65.0 x 47.9 x 7.00

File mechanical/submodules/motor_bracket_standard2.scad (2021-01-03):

plate_x_offset = 0;
plate_y_offset = -14;
plate_z_offset = 11;

plate_x_normal = 12;
plate_y_normal = 28;
plate_z_normal = 3;

peg_offset = 4.25;

module pegs(y_offset, x_offset = 0, r=3)
{
    translate([peg_offset+x_offset, y_offset, 3])
    {   
        cylinder(20, r, r, $fn=40);        
    }
}


module make_motor_mount(plate_x = plate_x_normal, plate_y = plate_y_normal, plate_z = plate_z_normal)
{
    translate([-peg_offset, 0, 0])
    {
        import("pololu-gear-motor-bracket-standard.stl");
        difference() 
        {
            translate([plate_x_offset, plate_y_offset, plate_z_offset]) {
                color("white") cube([plate_x,plate_y,plate_z],center=false);
            }
            union()
            {
                pegs(8.9);
                pegs(-8.9);
                pegs(0, 4.7, 1);
            }
        }
    }
}

//make_motor_mount();

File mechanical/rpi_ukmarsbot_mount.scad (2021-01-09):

//
//
//
use<submodules/motor_bracket_standard2.scad>;

// https://blog.prusaprinters.org/parametric-design-in-openscad_8758/
module rounded_plate(x, y, thickness, radius) {
    hull() {
        translate([radius, radius]) cylinder(r = radius, h = thickness, $fn=25);
        translate([x - radius, radius]) cylinder(r = radius, h = thickness, $fn=25);
        translate([x - radius, y - radius]) cylinder(r = radius, h = thickness, $fn=25);
        translate([radius, y - radius]) cylinder(r = radius, h = thickness, $fn=25);
    }
}
module four_posts(x, y, thickness, radius, r2, hole) {
    translate([radius, radius]) difference() { 
        cylinder(r = radius, h = thickness, $fn=25);
        if(hole) { cylinder(r = r2, h = thickness+0.1, $fn=25); }
    }
    translate([x - radius, radius]) difference() { 
        cylinder(r = radius, h = thickness, $fn=25);
        if(hole) { cylinder(r = r2, h = thickness+0.1, $fn=25); }
    }
    translate([x - radius, y - radius]) difference() { 
        cylinder(r = radius, h = thickness, $fn=25);
        if(hole) { cylinder(r = r2, h = thickness+0.1, $fn=25); }
    }
    translate([radius, y - radius]) difference() { 
        cylinder(r = radius, h = thickness, $fn=25);
        if(hole) { cylinder(r = r2, h = thickness+0.1, $fn=25); }
    }
}

module support(x, y, thickness, radius, f=25) {
    translate([x, y])
        cylinder(r = radius, h = thickness, $fn=f);
    
}

pizero_x = 65;
pizero_y = 30;
corner_r = 3;
hole_d = 2.75;
hole_r = hole_d / 2;
plate_height = 3;
cut_off = 0.1;
support_height_front = plate_height + 4;
support_height_mid = plate_height + 6;      // extra clearance for cables

// Basic Raspberry Pi support
module basic_pi_zero_support(hole, wire_cut = false, support_height=support_height_front)
{
    difference() {
        rounded_plate(pizero_x, pizero_y, plate_height, 3);
        
        // remove some material - to make it lighter
        // also misses mini-USB socket
        translate([0,0,-0.1]) { 
            hull /* union */ () {
                support(pizero_x/4, pizero_y/2, plate_height+0.2, 12, f=50);
                support(pizero_x/4*3, pizero_y/2, plate_height+0.2, 12, f=50);
            }
            if(wire_cut)
            {
                gap_width = pizero_x*0.6;
                translate([(pizero_x-gap_width)/2,0,0]) cube([gap_width, pizero_y/4, plate_height+0.2]);
            }
        }
    }
    four_posts(pizero_x, pizero_y, support_height, 3, hole_r, hole);

}

// Connection to UK MARS Bot
module connection_to_UKMARSBot(x, y, xh)
{
    r = 3;
    translate([-x/2 ,-y+0.1 ,0])
    {
        difference() {
            cube([x, y, plate_height]); //, 3);
            union() {
                hull() {
                    translate([-x/2-xh/2+r, -y/6, -0.1]) support(x, y, plate_height+0.2, r, 50);
                    translate([-x/2+xh/2-r, -y, -0.1]) support(x, y, plate_height+0.2, r, 50);
                    translate([-x/2+xh/2-r, -y/6, -0.1]) support(x, y, plate_height+0.2, r, 50);
                    translate([-x/2-xh/2+r, -y, -0.1]) support(x, y, plate_height+0.2, r, 50);
                }
                translate([3, 6.4, -0.1] ) cylinder(r=1.5, h = 30, $fn=25);
                translate([x-3, 6.4, -0.1] ) cylinder(r=1.5, h = 30, $fn=25);
            }
        }
    }
}

module connection_to_UKMARSBot_mid_plate(x, y, xh)
{
    translate([-xh/2, 0, 0]) {
        difference() {            
            translate([-x/2, -y/2, 0]) rounded_plate(x, y, plate_height, 3);
            translate([3, 0, -0.1] ) cylinder(r=1.5, h = 30, $fn=25);
        }
    }
    translate([xh/2, 0, 0]) {
        difference() {
            translate([-x/2, -y/2, 0]) rounded_plate(x, y, plate_height, 3);
            translate([-3, 0, -0.1] ) cylinder(r=1.5, h = 30, $fn=25);
        }
    }
}

distance_between_motor_mount_holes = 2.15 * 25.4; // according to ukmarsbot_dimensions.png
plate_y_normal = 28;
plate_top_height = 11+3;
height_above_top_motor_plate = 2;
plate_motor_mount_overlap = 2.5;



module complete_pi_plate_front(hole=true)
{
    translate([0, plate_y_normal/2-plate_motor_mount_overlap, plate_top_height+height_above_top_motor_plate])
    {
        translate([-pizero_x/2, 0, 0]) basic_pi_zero_support(hole);
        // This is the connection plate
        connection_to_UKMARSBot(distance_between_motor_mount_holes-3.5, 18, distance_between_motor_mount_holes-15.5);
    }
}

module complete_pi_plate_mid(hole=true)
{
    translate([0, 0, plate_top_height+height_above_top_motor_plate])
    {
        translate([-pizero_x/2, plate_y_normal/2-plate_motor_mount_overlap-26, 0]) basic_pi_zero_support(hole, true, support_height_mid);
        // This is the connection plate
        connection_to_UKMARSBot_mid_plate(12, 10, distance_between_motor_mount_holes-3.5);
    }
}

module motor_mounts(plate_z_new)
{
    // these are the motor mounts
    translate([-distance_between_motor_mount_holes/2, 0, 0]) {
        make_motor_mount(plate_z=plate_z_new);
    }
    
    translate([distance_between_motor_mount_holes/2, 0, 0]) {
        rotate([0, 0, 180]) {
            make_motor_mount(plate_z=plate_z_new);
        }
    }
}


// plate_z_new:
//      5 = touch connecting plate
//      plate_z_new = 7+1;
//      10 = above

// =======================================================
// Different options
//
SELECT_PI_PLATE_FRONT = false;
MOTOR_MOUNTS = true;
SELECT_PI_PLATE_MID = true;
// =======================================================

if(SELECT_PI_PLATE_FRONT)
{
    complete_pi_plate_front();
}
if(MOTOR_MOUNTS)
{
    motor_mounts(5);
}
if(SELECT_PI_PLATE_MID)
{
    complete_pi_plate_mid();
}

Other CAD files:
mechanical/other/pizero_holder.scad

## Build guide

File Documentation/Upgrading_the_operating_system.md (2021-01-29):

# Updating the Raspberry Pi OS

If you are running OTG, you need to make sure you have Internet sharing enabled. See [Sharing your Internet](Sharing_your_internet_OTG.md)

## Upgrading

For full details see: https://www.raspberrypi.org/documentation/raspbian/updating.md

The summary is:

First, update your system's package list by entering the following command:

    sudo apt update

Next, upgrade all your installed packages to their latest versions with the following command:

    sudo apt full-upgrade

Note that full-upgrade is used in preference to a simple upgrade, as it also picks up any dependency changes that may have been made.

It's worth checking with df -h that you have enough free disk space. The line with /dev/root mounted on / is the key line.

    pi@raspberrypi:~ $ df -h
    Filesystem      Size  Used Avail Use% Mounted on
    /dev/root        15G  1.4G   13G  10% /
    devtmpfs        184M     0  184M   0% /dev
    tmpfs           216M     0  216M   0% /dev/shm
    tmpfs           216M  8.5M  208M   4% /run
    tmpfs           5.0M     0  5.0M   0% /run/lock
    tmpfs           216M     0  216M   0% /sys/fs/cgroup
    /dev/mmcblk0p1  253M   47M  206M  19% /boot
    tmpfs            44M     0   44M   0% /run/user/1000

## Checking what Operating System you have

    pi@raspberrypi:~ $ uname -a
    Linux raspberrypi 5.4.83+ #1379 Mon Dec 14 13:06:05 GMT 2020 armv6l GNU/Linux

    pi@raspberrypi:~ $ cat /etc/os-release
    PRETTY_NAME="Raspbian GNU/Linux 10 (buster)"
    NAME="Raspbian GNU/Linux"
    VERSION_ID="10"
    VERSION="10 (buster)"
    VERSION_CODENAME=buster
    ID=raspbian
    ID_LIKE=debian
    HOME_URL="http://www.raspbian.org/"
    SUPPORT_URL="http://www.raspbian.org/RaspbianForums"
    BUG_REPORT_URL="http://www.raspbian.org/RaspbianBugs"

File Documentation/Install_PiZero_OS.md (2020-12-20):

# Installing Raspberry Pi OS on your SD card

Follow normal instructions on https://www.raspberrypi.org/software/ 

I typically instal the no GUI version, but if you or your users want a GUI they can VNC into, then the GUI version works - although there might be more memory use and if any saving to SD card happens this tend to slow down response speed AND it might take more current from the 5v line.

REMEMBER: GUI uses more processing, therefore more current. I therefore strongly suggest no GUI versions. (But see https://raspi.tv/2017/how-much-power-does-pi-zero-w-use )

If you are using the Rapberry Pi Imager, these are the options to select:

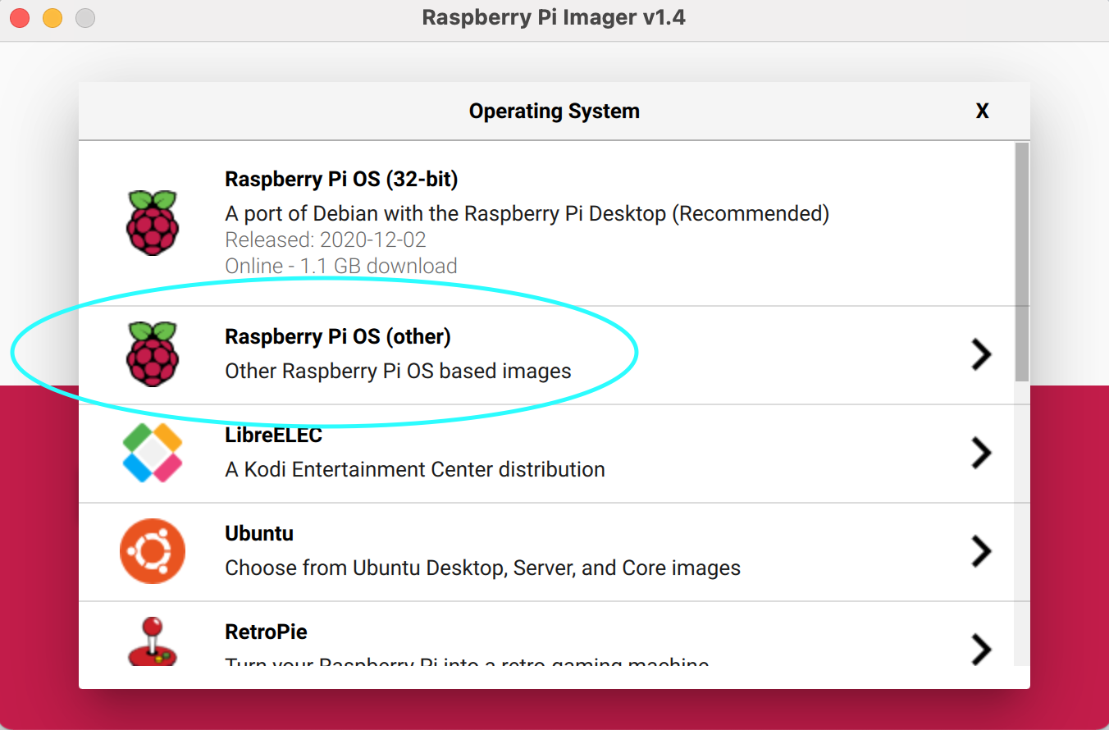
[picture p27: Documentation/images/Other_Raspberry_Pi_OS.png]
Select Other Raspberry Pi

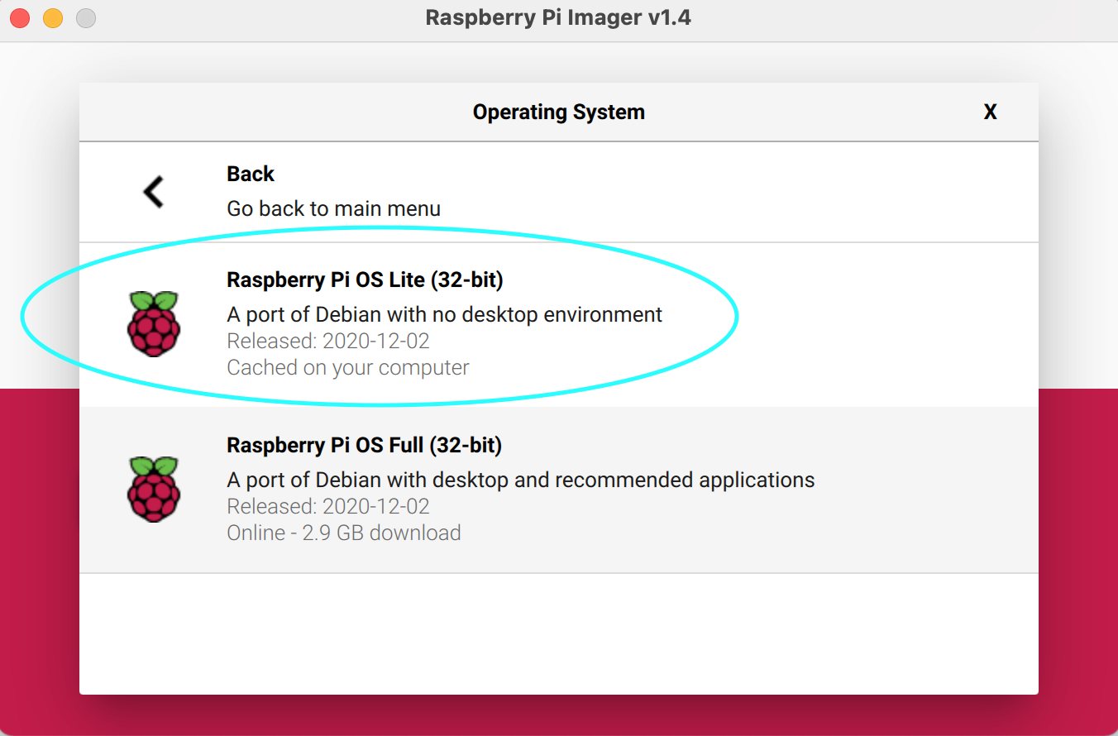
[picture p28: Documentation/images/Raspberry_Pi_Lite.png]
Select Raspberry Pi Lite


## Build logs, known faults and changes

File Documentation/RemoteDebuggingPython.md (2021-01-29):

# Remote Debugging Python

## Items to cover

A serial or SSH connection

Eclipse with PyDev

Synchronisng Code

## References

https://www.pydev.org/manual_adv_remote_debugger.html

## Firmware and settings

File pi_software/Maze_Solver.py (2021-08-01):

#!/usr/bin/env python3
# -*- coding: utf-8 -*-
#
""" The program simply prints some data from the Arduino 
    Nano then quits.
    
    Intended to run on a Raspberry Pi on the actual robot.
        
    The serial port are set from robot_settings.py.
"""
#
# Copyright (c) 2021 Rob Probin.
#               (Some items taken from Vison2/Dizzy platform 2016)
# All original work.
#
# This is licensed under the MIT License. Please see LICENSE.
#
#
# NOTES
# * Coding Convention PEP-8   https://www.python.org/dev/peps/pep-0008/
# * Docstrings PEP-257   https://www.python.org/dev/peps/pep-0257/

from robot_libs.general_utils import version_check
from robot_libs.ukmarsey_commands import UkmarseyCommands
from robot_libs.ukmarsey_commands import InterpreterError, SerialSyncError
from robot_libs.ukmarsey_utils import wait_for_button_press, battery_check
from robot_libs.ukmarsey_utils import setup_left_and_right_sensor_LEDs, change_left_sensor_led, change_right_sensor_led
from robot_libs.ukmarsey_utils import wait_for_front_sensor
from robot_libs.Raspberry_Pi_Lib import define_gpio_ports, get_buzzer, beep

import robot_settings
import time

################################################################
#
# Functions
#

def robot_print_data_setup():
    ''' do basic setup '''
    commands = UkmarseyCommands(robot_settings.serial_port, robot_settings.SNOOP_SERIAL_DATA)
    commands.reset_arduino()
    
    setup_left_and_right_sensor_LEDs(commands)
    return commands

def robot_print_data_main(commands):
    """
    Main robot function 
    """
    bat_voltage = battery_check(commands)
    print("Battery Voltage", bat_voltage, "volts")

    switch_state = commands.get_switches()
    print("Switches selected as", "{0:04b}".format(switch_state))
            
    print("Complete Print Data")
    
def do_menu(commands):
    print()
    print("Menu")
    
    switch_state = wait_for_button_press(commands)

    print("Switches selected as", "{0:04b}".format(switch_state))

    battery_check(commands)
    
        
def wait_for_wave(commands):
    print()
    print("Wait for wave")
    wait_for_front_sensor(commands)

def do_run(commands):
    print()
    print("Run")
    time.sleep(1)

def main():
    ''' This captures specific exceptions and cleans up and get's the robot
        running again
    '''
    version_check()
    define_gpio_ports()
    beep(0.1)
    
    try:
        commands = robot_print_data_setup()
        setup_left_and_right_sensor_LEDs(commands)
        robot_print_data_main(commands)
        
        while True:
            do_menu(commands)
            get_buzzer().beep(0.05, 0.05, 1)
            wait_for_wave(commands)
            
            do_run(commands)
            
    except InterpreterError as ie:
        print(type(ie), ie)
        # TODO: Recover connection and stop robot
    except SerialSyncError as sse:
        print(type(sse), sse)


        # TODO: Recover connection and stop robot
'''        global port_snooper_copy
        port_snooper_copy.print_all()
   '''

if __name__ == "__main__":
    main()

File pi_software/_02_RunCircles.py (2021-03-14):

#!/usr/bin/env python3
# -*- coding: utf-8 -*-
#
'''

This program spins on the spot and uses the data to calibrate the three
sensors, assuming it's in a U shaped start position of a standard maze cell.

Various robot parameters including the serial port are in robot_settings.py.

Created on 4 Mar 2021

@author: Rob Probin
'''
#
# Copyright (c) 2021 Rob Probin.
#               (Some items taken from Vison2/Dizzy platform 2016)
# All original work.
#
# This is licensed under the MIT License. Please see LICENSE.
#
# NOTES
# * Coding Convention PEP-8   https://www.python.org/dev/peps/pep-0008/
# * Docstrings PEP-257   https://www.python.org/dev/peps/pep-0257/

from robot_libs.general_utils import version_check
from robot_libs.ukmarsey_commands import UkmarseyCommands
from robot_libs.ukmarsey_commands import InterpreterError, SerialSyncError
from robot_libs.ukmarsey_utils import wait_for_button_press, battery_check
from robot_libs.ukmarsey_utils import setup_left_and_right_sensor_LEDs, change_left_sensor_led, change_right_sensor_led
import robot_settings
import time
import math

################################################################
#
# Configuration constants
#

SPEED_TO_CIRCLE = 250    # in mm/s
CIRCLE_DIAMETER = 300        # in mm = 30cm

################################################################
#
# Functions
#

def robot_run_circles_setup():
    ''' do basic setup '''
    commands = UkmarseyCommands(robot_settings.serial_port, robot_settings.SNOOP_SERIAL_DATA)
    commands.reset_arduino()
    setup_left_and_right_sensor_LEDs(commands)
    return commands

def robot_run_circles_test_main(commands):
    """
    Main robot function 
    """
    bat_voltage = battery_check(commands)
    print("Battery Voltage", bat_voltage, "volts")

    switch_state = wait_for_button_press(commands)

    print("Switches selected as", "{0:04b}".format(switch_state))

    battery_check(commands)
    time.sleep(0.5)
    
    v_speed = SPEED_TO_CIRCLE
    
    # we need to calculate the required angular velocity
    circumference_distance = math.pi * CIRCLE_DIAMETER
    time_to_complete_circumference = circumference_distance / v_speed 
    # literally 360 divided by time
    # e.g. if the speed takes 4 seconds to complete the distance of the circumfrence
    # then we need 360/4, or 90 degrees per second
    w_angular_velocity_in_degrees_per_sec = 360 / time_to_complete_circumference

    # Figure out direction: 
    #  - Switch lowest bit Clear = anticlockwise
    #  - Switch lowest bit Set = clockwise
    if switch_state & 1:
        print("Clockwise")
        w_angular_velocity_in_degrees_per_sec = -w_angular_velocity_in_degrees_per_sec
        change_right_sensor_led(commands, True)
    else:
        print("Anticlockwise")
        change_left_sensor_led(commands, True)
    
    commands.set_speed_and_rotation(v_speed, w_angular_velocity_in_degrees_per_sec)
    
    # Loop where do we something ... 
    while commands.get_switches() != 16:
        time.sleep(0.05)
        battery_check(commands)
    
    commands.stop_motors();
    time.sleep(1)
    print("Completed Circle Test")


def main():
    ''' This captures specific exceptions and cleans up and get's the robot
        running again
    '''
    version_check()
    try:
        commands = robot_run_circles_setup()
        while True:
            robot_run_circles_test_main(commands)
    except InterpreterError as ie:
        print(type(ie), ie)
        # TODO: Recover connection and stop robot
    except SerialSyncError as sse:
        print(type(sse), sse)


if __name__ == "__main__":
    main()

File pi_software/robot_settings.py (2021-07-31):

#!/usr/bin/env python3
# -*- coding: utf-8 -*-
#
""" Main Control file for UKMarsBot Robot with an Arduino Nano co-processor.
    Intended to run on a Raspberry Pi on the actual robot.
"""
#
# Copyright (c) 2016-2021 Rob Probin.
#               (Some items taken from Vison2/Dizzy platform)
# All original work.
#
# This is licensed under the MIT License. Please see LICENSE.
#
# NOTES
# * Coding Convention PEP-8   https://www.python.org/dev/peps/pep-0008/
# * Docstrings PEP-257   https://www.python.org/dev/peps/pep-0257/

from sys import platform
from robot_libs.Raspberry_Pi_Lib import is_raspberry_pi

################################################################
#
# Debug configuration
#

SNOOP_SERIAL_DATA = False        # good but slow
INHIBIT_LOW_BATTERY_SHUTDOWN = False    # stop shutdown. NOTICE: Overriden for Windows, Mac below.
USE_OK_FOR_ALL_COMMANDS = True # slows down replies, but ensures all replies are acknowledged

################################################################
#
# Select correct serial port
#    ... usually Raspberry Pi
#        but allows connection of Arduino Nano directly to computer for testing
#
# For Raspberry Pi this shoudl work 'out-of-the-box', but for other platforms
# you'll need to adjust the serial report depending on where the Nano got
# attached...
if platform == "linux" or platform == "linux2":
    if is_raspberry_pi():
        # Raspberry Pi Serial Port
        #
        # See this for full details:
        #
        # https://www.raspberrypi.org/documentation/configuration/uart.md
        #
        # On the Raspberry Pi, one UART is selected to be present on GPIO 14 (transmit)
        # and 15 (receive) - this is the primary UART. By default, this will also be the
        # UART on which a Linux console may be present. Note that GPIO 14 is pin 8 on the
        # GPIO header, while GPIO 15 is pin 10.
        #
        #
        # Model                 first PL011 (UART0)     mini UART
        # Raspberry Pi Zero     primary                 secondary
        # Raspberry Pi Zero W  secondary (Bluetooth)     primary
        #
        # Linux device     Description
        # /dev/ttyS0       mini UART
        # /dev/ttyAMA0     first PL011 (UART0)
        # /dev/serial0     primary UART
        # /dev/serial1     secondary UART
        #
        # Note: /dev/serial0 and /dev/serial1 are symbolic links which point to either
        # /dev/ttyS0 or /dev/ttyAMA0.

        #  primary UART om pins 8 & 10 (GPIO14/15)
        serial_port = "/dev/serial0"

    else:
        # Desktop Linux Machine
        serial_port = "/dev/ttyS1"
        serial_port = "/dev/ttyUSB0"

elif platform == "darwin":
    # OS X - Mac Serial port
    #serial_port = "/dev/cu.usbserial-1420"
    #serial_port = "/dev/cu.usbserial-1410"
    serial_port = "/dev/cu.usbserial-14240"
    INHIBIT_LOW_BATTERY_SHUTDOWN = True

elif platform == "win32":
    # Windows...
    serial_port = "COM3"  #  select your Windows serial port here
    INHIBIT_LOW_BATTERY_SHUTDOWN = True

else:
    raise ValueError("Unknown platform")


################################################################
#
# Constants
#

# Set this to a resonable value
BATTERY_VOLTAGE_TO_SHUTDOWN = 6.5   # volts

# the default values for the front sensor when the robot is backed up to a wall
FRONT_REFERENCE = 44
# the default values for the side sensors when the robot is centred in a cell
LEFT_REFERENCE = 38
RIGHT_REFERENCE = 49

# the values above which, a wall is seen
FRONT_WALL_THRESHOLD = FRONT_REFERENCE / 20  # minimum value to register a wall
LEFT_WALL_THRESHOLD = LEFT_REFERENCE / 2     # minimum value to register a wall
RIGHT_WALL_THRESHOLD = RIGHT_REFERENCE / 2   # minimum value to register a wall

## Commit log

2021-01-03 Baseline - old mount
    [motor_bracket_standard2.scad, pizero_holder.scad, pololu-gear-motor-bracket-standard.stl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]
2021-01-03 Work in progress
    [rpi_ukmarsbot_mount.scad]
2021-01-03 Changes for first prototype
    [motor_bracket_standard2.scad, rpi_ukmarsbot_mount.scad]
2021-01-04 Added STL files for Robot mount
    [motor_mounts_only.stl, pi_plate.stl]
2021-01-04 Added Instructions for mechanical mounting.
2021-01-09 Added a mid-mounting option along with the front mounting option.
    [rpi_ukmarsbot_mount.scad]
2021-01-09 Extra clearance to miss cables
    [rpi_ukmarsbot_mount.scad]
2021-01-09 Swap to just extending supports for mid-placement version.
    [rpi_ukmarsbot_mount.scad]
2021-01-09 Made cut-out for wires for mid-section.
    [rpi_ukmarsbot_mount.scad]
2021-01-09 Added STL for mid-mount.
    [pi_plate_mid_placement.stl]
2021-01-09 Added documentation on new Mid mount design.
2021-01-09 Add pictures on wiring to connection pages.
2021-01-30 Added basic Ardunino Nano reset sequence
    [Raspberry_Pi_Lib.py]
2021-01-31 Initial communication with Arduino
2021-02-01 Fix todo: items so they appear in Eclipse’s TASK list.
2021-02-01 Added sensor read command.
2021-02-06 Make LEDs flash at same rate so it doesn’t look like a comms problem.
2021-02-06 Removed sensor change detect ‘*’ - no longer required.
2021-02-08 Support for new sensor read commands.
2021-02-08 Once in the main loop, sensors detects distance and shows on 3 LEDs. LEDs flash until button is pressed, and then gets into main loop.
2021-02-11 Support new sensor readings (6 rather than 4). Changed version to v1.3 and baud rate back to 115200.
2021-03-07 Changed robot_control into separate Sensor test example. Also changed functions into library functions.
2021-03-07 General tidy up of SensorTest: * Made loop outer, so that we can have a multi-function script. * Factored battery_check into utility function * Allowed desktop builds to run off USB voltage * Linked 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
2021-03-14 Write the battery voltage on shutdown
2021-03-14 Support for battery shutdown
2021-03-14 Lower battery shutdown voltage a bit
2021-03-14 Added simple app to print data from Nano.
2021-07-31 Code to parse ok. Also includes sensor enable/disable.
2021-07-31 Provisional wait for front sensor.
